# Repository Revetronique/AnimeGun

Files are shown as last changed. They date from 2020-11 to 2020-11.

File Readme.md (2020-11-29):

# アニメ銃 (ストロボスコープ式映写機)
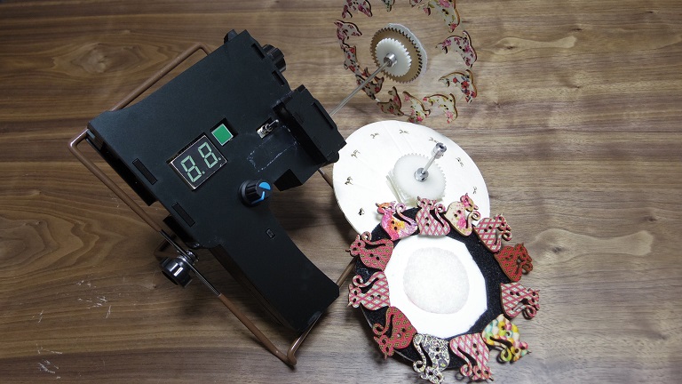
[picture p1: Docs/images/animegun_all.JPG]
Top Image

## 目次
- [アニメ銃 (ストロボスコープ式映写機)](#アニメ銃-ストロボスコープ式映写機)
  - [目次](#目次)
- [概要](#概要)
- [準備するもの](#準備するもの)
  - [本体](#本体)
  - [円板](#円板)
- [使い方](#使い方)
  - [ボタン一覧](#ボタン一覧)
  - [基本](#基本)
  - [詳細](#詳細)
    - [パラメータ設定](#パラメータ設定)
    - [設定モード](#設定モード)
    - [設定方法](#設定方法)
    - [ファームウェア書き換え](#ファームウェア書き換え)
- [免責事項](#免責事項)
- [開発者](#開発者)
# 概要
影絵でアニメーション映像を見せる映写機です。

電源を入れて、壁に向かって引き金のボタンを押すことで、壁にアニメーションが映し出されます。

アニメのコマを描いた円板をモーターで回し、LEDのストロボ発光でアニメーションを移す仕組みです。
# 準備するもの
## 本体
- Arduino UNO R3
- LED
  - 単色を想定(主に白色)
  - パワーLED(5V, 1W or 3W)にも対応
- 専用シールド
  - [回路およびプリント基板(Eagle用)](./Circuit)
  - 回路の詳細については、[回路についてのドキュメント](./Docs/Document_Circuit.md)を参照
- 筐体
  - アクリル板(厚さ3mm)をレーザーカッターで切断して、各パーツを積み重ねて制作
  - 筐体用のフレームは[Frameフォルダ](./Frame)を参照
  - 詳細は、[筐体についてのドキュメント](./Docs/Document_Frame.md)を参照
  - **試作段階のため、回路が筐体に収まらないなどの問題が生じる可能性があります**
- ACアダプタ(出力：DC12V, 1A以上)
## 円板
詳細は[円板についてのドキュメント](./Docs/Document_Plate.md)を参照。
# 使い方
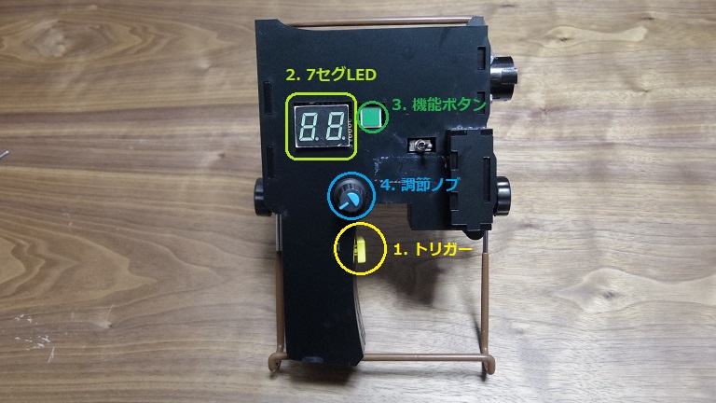
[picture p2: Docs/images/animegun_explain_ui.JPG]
Front Image

## ボタン一覧
1. **トリガー**：押すことでアニメを動かします(ストロボ発光+モーター駆動)
2. 7セグLED：設定モード([後述](#設定モード))やアニメに関するパラメータを表示
3. 機能ボタン：押すと設定モードを変更
4. **調節ノブ**：回すことでパラメータを調節

また、トグルスイッチでモーター回転の有効/無効を切り替えられます(右に倒すと有効)。ファームウェアの書き換え中など、モーターを回したくない時は左に倒してください。
## 基本
1. モーターにアニメ用の円板を付けます
2. 本体後ろのDCジャックに、上記のACアダプタから電源を供給
3. 銃口を壁に向けてトリガーを引くと、アニメーションが流れます
4. 調節ノブを回すと、アニメーションの速さを変えられます
## 詳細
### パラメータ設定
機能ボタンと調節ノブを使って、アニメーションに関する4種類のパラメータを調整できます。選択したパラメータと数値は7セグLEDで確認できます。
### 設定モード
パラメータの種類は以下の通り。
- sp(回転速度)：モーターの回転数(rpm)。数値は8~60
- dg(角度調節)：円板の角度調節。ずれの相殺に使います
- br(明るさ)：LEDの明るさ調整。0~25までの26段階
- fr(フレーム数)：アニメのコマ数
### 設定方法
起動時は、sp(回転速度)がセットされています。

ボタンを押すと、sp->dg->bf->fr の順に切り替わります。ボタンを押して0.5秒程度、選んだパラメータ名が7セグLEDに表示されます。

表示が数値に切り替わったら、調節ノブでパラメータを調節できます。
### ファームウェア書き換え
本体のファームウェア(Arduinoスケッチ)を書き換えたい場合は、背面のUSBコネクタでArduino IDEの入ったPCなどと接続します。ケーブルはUSB(ABタイプ)を使用します。
# 免責事項
- **使うときは人に向けないでください。特にパワーLEDを搭載する場合、失明の恐れがあります**
- 本体を振り回さないでください。ケガや破損の恐れがあります。
- モーターの回転中は、円板に触れないよう注意してください。思わぬケガの元となります。
- ファームウェア書き換え時は、書き込み用の機器と接続する前に、本体の電源を外してください。また、**接続中はトリガーを押さないでください**。
- 円板を付け替える際も、電源を外してから作業してください。
- 15V以上の電圧を絶対にかけないでください。
  - 出力電源は、12V,1A出力のACアダプタ推奨。
- 上記の項目の他、組み立て時や使用中などにおける利用者のあらゆる事故・不具合に対して、開発者は責任を負いません。

# 開発者
Revetronique
- [Web](https://revetronique.com/)
- [Twitter](https://twitter.com/Revetronique)
- [Instagram](https://www.instagram.com/revetronique/)

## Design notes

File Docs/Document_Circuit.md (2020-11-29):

# 回路について
## 概要
アニメ銃に組み込むArduino用シールドです。[Circuit](../Circuit)内にデータを保管してます。
## 回路図
本体用シールド

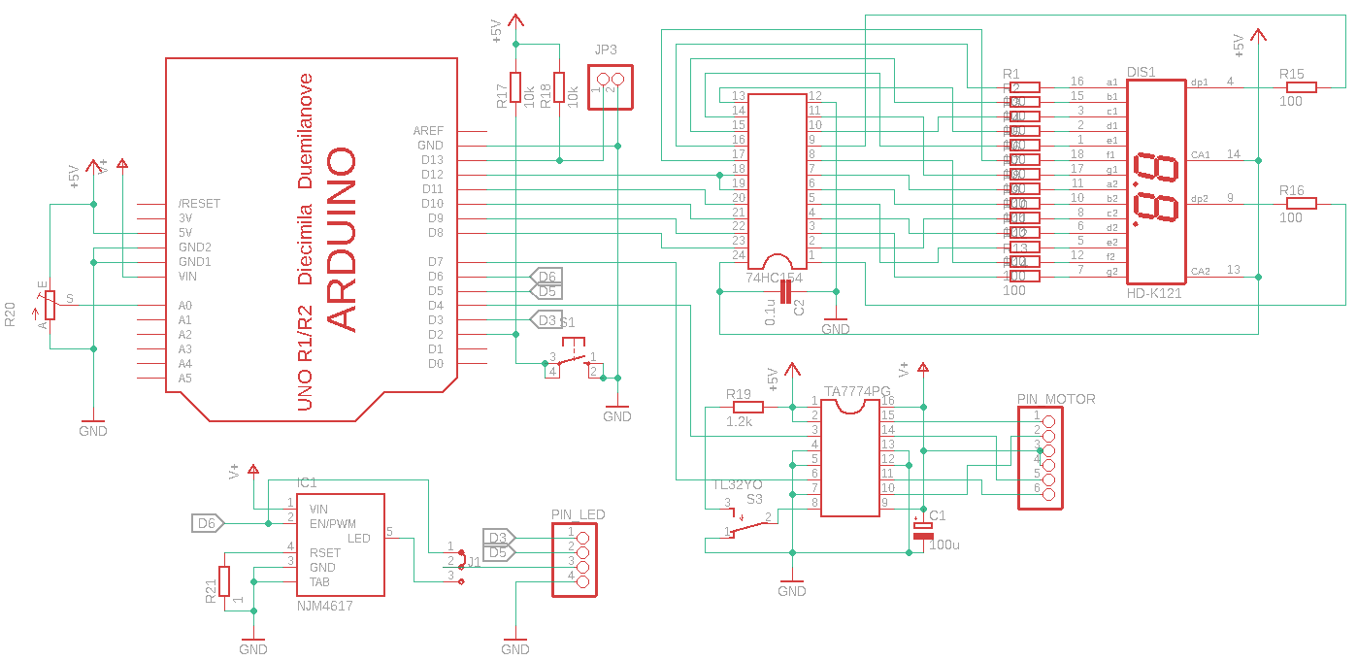
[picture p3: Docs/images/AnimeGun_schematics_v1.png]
Schematics


パワーLED用ハイサイドスイッチ

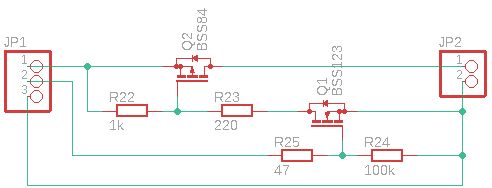
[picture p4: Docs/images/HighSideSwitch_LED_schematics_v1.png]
Highside

## 基板パターン(未使用)
基板配線

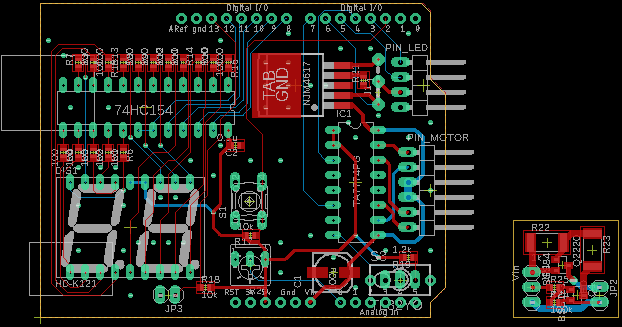
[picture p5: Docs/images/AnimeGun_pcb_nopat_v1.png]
PCB_nopat


ベタパターンあり

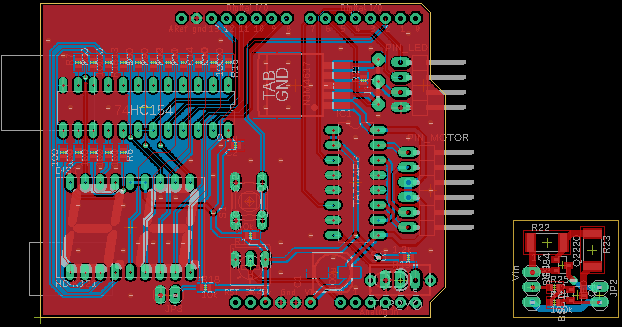
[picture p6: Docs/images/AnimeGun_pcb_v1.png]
PCB

## ファイル内容
- [回路図(Eagle)](../Circuit/AnimeGun_v1.sch)
- [パターン図(Eagle)](../Circuit/AnimeGun_v1.brd)
- [部品一覧](../Circuit/AnimeGun_bom_v1.txt)
## 使い方
1. Eagleでプロジェクトを新規作成
2. Eagleプロジェクトに上記ファイル2種類を読み込ませます
3. 必要に応じて、ライブラリをインストールしてください(Arduino、7セグLEDなど)
4. LEDドライバの部品のみ、既存ライブラリ(on-semiconductor.lbrのCAT4101)をもとに自作しました。CAT4101をコピーしてピン1と2を入れ替えるだけです。
## 注意点
- Eagleファイルは、試作した回路をもとに**後から作成した**ものです。試作品とは一部実装が異なる部分があります。
- PCBは、ユニバーサル基板で手付けした回路を元にEagleで書き起こしたもので、筐体との寸法や動作が合わない可能性があります
- J1はLEDドライバの実装を切り替えます
  - パワーLED用ドライバを実装する場合は、ピン2と3をショート
  - ドライバを実装しない/外部で接続する場合は、ピン1と2をショート
- LEDドライバの電流は、R21の抵抗値(=0.2/LED電流(A))で設定します。
- パワーLED用ハイサイドスイッチは、試作品で使用したLEDドライバへの電源制御用回路です(試作時は、秋月電子のLEDドライバ(3W)と出力ピン(D6)の間に接続)
  - シールドにLEDドライバを実装する場合は不要です
  - PWMで出力電圧を調整します
  - 電源は、ACアダプタの出力プラグを分岐するなどで接続してください
- Eagleで利用したタクトスイッチ(S1)では筐体に入らない可能性があります。秋月電子のボタン付タクトスイッチ(緑色)を実装してください
- 可変抵抗(R20)は、配線をのばして可変抵抗用の穴にさして固定します
- PIN_LEDはフルカラーLED用にPWMピン3つ(D3,5,6)をつないでいますが、通常は下から2番目のピンD6だけを使います

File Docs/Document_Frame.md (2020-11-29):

# 筐体について
## 概要
[Readme](../Readme.md)の写真にある筐体は、3mm厚のアクリル板をレーザーカッターでカットし、それぞれのパーツを積み重ねる形で作られています。
## ファイル内容
- [Adobeイラストレータファイル](../Frame/AnimeGun_frame.ai)
- [epsファイル(レーザーカッター出力用)](../Frame/AnimeGun_frame.ai)
## 使い方
1. epsファイルをレーザーカッターに読み込ませます
2. 3mm厚のアクリル板をレーザーカッターにセットします
3. それぞれの部品を貼りあわせます。接着剤はアクリサンデーが一般的です
## 注意点
- 試作段階のため、回路が筐体に収まらないなどの問題が生じる可能性があります
- パーツの貼り合わせる順番に注意してください
- パワーLED用の固定器具はありません。ご自身で作成してください

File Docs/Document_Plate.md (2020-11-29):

# アニメ用の円板について
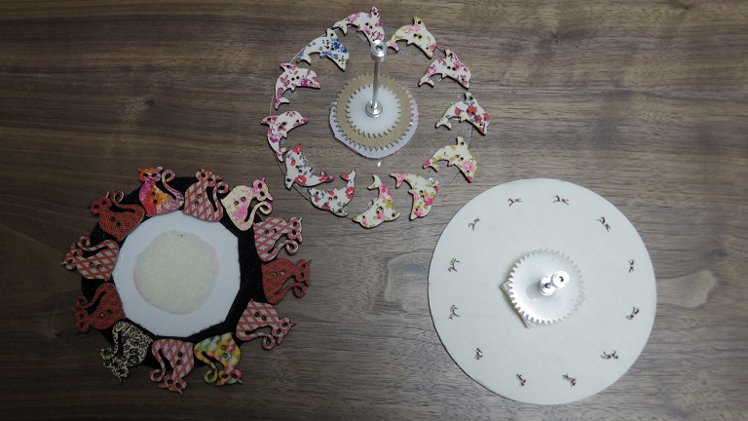
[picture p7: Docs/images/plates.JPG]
Front Image

## 概要
- サイズは直径12㎝
  - LEDの中心~モーター軸間の距離が 5cm のため
  - 筐体の変更などでLEDとモーターの距離が変われば、適切なサイズも変わります
- 素材は特に決まっていません
  - ただし、以下の条件を満たすものをお勧めします。
    - 自分で簡単に加工できる
    - 重すぎない
    - 立てたときに、曲がったりしなったりしない
  - なお制作時は、スチレンボードとアクリル板をそれぞれレーザーカッターで切り出しました。
## 準備
1. 直径12cmの円板を用意
2. アニメーションのパターン作成
   - パラパラ漫画の要領で、コマ数と絵のパターンを作ります
     - 12コマ位でパターンを用意するといい感じに配置できます
   - 「フェナキストスコープ」や「ゾートロープ」で画像検索するのもおすすめです
3. 円板にパターンを加工
   1. 光の像
      - 円板に等間隔でパターンの穴をくりぬきます
      - レーザーカッターなら円板自体も含めて綺麗に切り出せます。その場合、Adobeイラストレータなどでアニメのコマを円盤に配置したデータを作り、epsファイルを書き出す必要があります
      - 手作業の場合は、厚紙やスチレンボードなどをカッターで切るのが簡単かと思います
   2. 影絵
      - 各コマを切り取ったパーツを串につけ、モーター軸を中心に等間隔で並べると影絵ができます
      - アクリルなど透明な板に、小さなパーツを両面テープを使って貼り付ける方法もあります(画像中央の円板が該当)
4. シャフトと取り付け器具(カップリング)の設置
      - モーター軸は3mmなので、円板に取り付けるシャフトも3㎜幅がおすすめ
      - 円板の中心に、シャフトと同じ直径の穴をあけておきます
      - 円板にシャフトを差して固定します
      - シャフトの反対側に、モーターと結合するための部品をつけます
      - ジョイント用の部品は、[ストッパー](https://www.sengoku.co.jp/mod/sgk_cart/detail.php?code=4AJD-B5EA)や[インラインカラー](https://www.sengoku.co.jp/mod/sgk_cart/detail.php?code=5ALD-CJE7#)を使うといいでしょう
5. モーターとシャフトのジョイント

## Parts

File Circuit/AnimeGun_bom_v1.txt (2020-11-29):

Partlist exported from C:/Users/kokit/OneDrive/ドキュメント/EAGLE/projects/AnimeGun/AnimeGun-v1.sch at 2020/11/28 15:33

Part      Value          Device             Package        Description                                     MF MPN           OC_FARNELL OC_NEWARK POPULARITY SPICEPREFIX
74HC154                  DIL24-3            DIL24-3        Dual In Line                                                                          0                     
C1        100u           CPOL-EU153CLV-0605 153CLV-0605    POLARIZED CAPACITOR, European symbol                                                  5          C          
C2        0.1u           C-EUC0603          C0603          CAPACITOR, European symbol                                                            73         C          
DIS1      HD-K121        HD-K121            HDSP-R         LED DISPLAY                                                      unknown    unknown   0                     
IC1       NJM4617        NJM4617            TO263_5        1A Constant-Current LED Driver with PWM Dimming    CAT4101TV-T75 1718452    08R5264                         
J1                       J2X2MM             04C            Jumper switch 2 x 2.5 mm                                                                                    
JP1       Vin            PINHD-1X3          1X03           PIN HEADER                                                                            92                    
JP2       LED            PINHD-1X2          1X02           PIN HEADER                                                                            98                    
JP3                      PINHD-1X2          1X02           PIN HEADER                                                                            98                    
PIN_LED                  PINHD-1X4/90       1X04/90        PIN HEADER                                                                            9                     
PIN_MOTOR                PINHD-1X6/90       1X06/90        PIN HEADER                                                                            10                    
Q1        BSS123         BSS123             SOT23          N-CHANNEL MOS FET                                                                                           
Q2        BSS84          BSS84              SOT23          P-CHANNEL MOS FET                                                                                           
R1        100            R-EU_R0603         R0603          RESISTOR, European symbol                                                             70         R          
R2        100            R-EU_R0603         R0603          RESISTOR, European symbol                                                             70         R          
R3        100            R-EU_R0603         R0603          RESISTOR, European symbol                                                             70         R          
R4        100            R-EU_R0603         R0603          RESISTOR, European symbol                                                             70         R          
R5        100            R-EU_R0603         R0603          RESISTOR, European symbol                                                             70         R          
R6        100            R-EU_R0603         R0603          RESISTOR, European symbol                                                             70         R          
R7        100            R-EU_R0603         R0603          RESISTOR, European symbol                                                             70         R          
R8        100            R-EU_R0603         R0603          RESISTOR, European symbol                                                             70         R          
R9        100            R-EU_R0603         R0603          RESISTOR, European symbol                                                             70         R          
R10       100            R-EU_R0603         R0603          RESISTOR, European symbol                                                             70         R          
R11                      R-EU_R0603         R0603          RESISTOR, European symbol                                                             70         R          
R12       100            R-EU_R0603         R0603          RESISTOR, European symbol                                                             70         R          
R13       100            R-EU_R0603         R0603          RESISTOR, European symbol                                                             70         R          
R14       100            R-EU_R0603         R0603          RESISTOR, European symbol                                                             70         R          
R15       100            R-EU_R0603         R0603          RESISTOR, European symbol                                                             70         R          
R16       100            R-EU_R0603         R0603          RESISTOR, European symbol                                                             70         R          
R17       10k            R-EU_R0603         R0603          RESISTOR, European symbol                                                             70         R          
R18       10k            R-EU_R0603         R0603          RESISTOR, European symbol                                                             70         R          
R19       1.2k           R-EU_R0603         R0603          RESISTOR, European symbol                                                             70         R          
R20                      TRIM_EU-B25U       B25U           POTENTIOMETER                                                                                               
R21       1              R-EU_R0603         R0603          RESISTOR, European symbol                                                             70         R          
R22       1k             R-EU_R2512         R2512          RESISTOR, European symbol                                                             0          R          
R23       220            R-EU_R2512         R2512          RESISTOR, European symbol                                                             0          R          
R24       100k           R-EU_R0603         R0603          RESISTOR, European symbol                                                             70         R          
R25       47             R-EU_R0603         R0603          RESISTOR, European symbol                                                             70         R          
S1                       10-XX              B3F-10XX       OMRON SWITCH                                       B3F-1000      176432     36M3542   72                    
S3        TL32YO         TL32YO             TL3XYO         TINY SWITCH ON - MOM                                                                  1                     
TA7774PG                 DIL16              DIL16          Dual In Line / Socket                                                                 2                     
U1        ARDUINO-NOHOLE ARDUINO-NOHOLE     ARDUINO-NOHOLE Arduino Diecimila/Duemilanove

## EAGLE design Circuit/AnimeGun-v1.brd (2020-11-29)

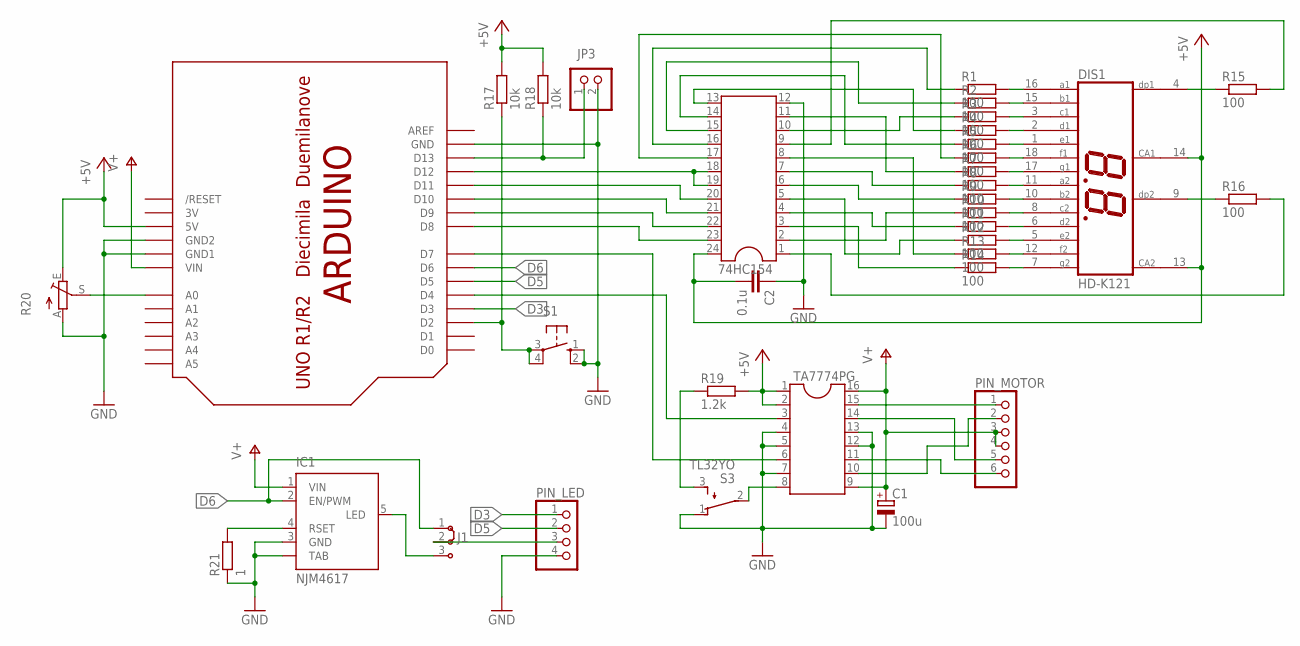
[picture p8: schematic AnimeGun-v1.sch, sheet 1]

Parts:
74HC154: DIL24-3
C1: 100u; 153CLV-0605
C2: 0.1u; C0603
DIS1: HD-K121; HDSP-R
IC1: NJM4617; TO263_5
J1: J2X2MM; 04C
JP3: PINHD-1X2; 1X02
PIN_LED: PINHD-1X4/90; 1X04/90
PIN_MOTOR: PINHD-1X6/90; 1X06/90
R1, R2, R3, R4, R5, R6, R7, R8, R9, R10, R12, R13, R14, R15, R16: 100; R0603
R11: R-EU_R0603; R0603
R17, R18: 10k; R0603
R19: 1.2k; R0603
R20: TRIM_EU-B25U; B25U
R21: 1; R0603
S1: 10-XX; B3F-10XX
S3: TL32YO; TL3XYO
TA7774PG: DIL16
U1: ARDUINO-NOHOLE

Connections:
3V: U1.3V
+5V: 74HC154.24, C2.2, DIS1.13 (CA2), DIS1.14 (CA1), R17.2, R18.2, R19.2, R20.E, TA7774PG.1, TA7774PG.2, U1.5V
D3: PIN_LED.1, U1.D3
D5: PIN_LED.2, U1.D5
D6: IC1.2 (EN/PWM), J1.1, U1.D6
GND: 74HC154.12, C1.-, C2.1, IC1.3 (GND), IC1.TAB, JP3.2, PIN_LED.4, R20.A, R21.1, S1.1 (S), S1.2 (S1), S3.1 (O), TA7774PG.4, TA7774PG.5, TA7774PG.7, TA7774PG.12, TA7774PG.13, U1.GND, U1.GND1, U1.GND2
unnamed: R17.1, S1.3, S1.4 (P1), U1.D2
unnamed: DIS1.16 (A1), R1.2
unnamed: DIS1.15 (B1), R2.2
unnamed: DIS1.3 (C1), R3.2
unnamed: DIS1.2 (D1), R4.2
unnamed: DIS1.1 (E1), R5.2
unnamed: DIS1.18 (F1), R6.2
unnamed: DIS1.17 (G1), R7.2
unnamed: DIS1.11 (A2), R8.2
unnamed: DIS1.10 (B2), R9.2
unnamed: DIS1.8 (C2), R10.2
unnamed: DIS1.6 (D2), R11.2
unnamed: DIS1.5 (E2), R12.2
unnamed: DIS1.12 (F2), R13.2
unnamed: DIS1.7 (G2), R14.2
unnamed: DIS1.4 (DP1), R15.1
unnamed: DIS1.9 (DP2), R16.1
unnamed: 74HC154.1, R16.2
unnamed: 74HC154.2, R10.1
unnamed: 74HC154.3, R14.1
unnamed: 74HC154.4, R11.1
unnamed: 74HC154.5, R12.1
unnamed: 74HC154.6, R9.1
unnamed: 74HC154.7, R8.1
unnamed: 74HC154.8, R13.1
unnamed: 74HC154.9, R15.2
unnamed: 74HC154.10, R3.1
unnamed: 74HC154.11, R7.1
unnamed: 74HC154.13, R4.1
unnamed: 74HC154.14, R5.1
unnamed: 74HC154.15, R2.1
unnamed: 74HC154.16, R1.1
unnamed: 74HC154.17, R6.1
unnamed: 74HC154.18, 74HC154.19, U1.D12
unnamed: TA7774PG.6, U1.D7
unnamed: 74HC154.20, U1.D11
unnamed: 74HC154.21, U1.D10
unnamed: 74HC154.22, U1.D9
unnamed: 74HC154.23, U1.D8
unnamed: TA7774PG.3, U1.D4
unnamed: JP3.1, R18.1, U1.D13
unnamed: S3.2, TA7774PG.8
unnamed: PIN_MOTOR.6, TA7774PG.11
unnamed: PIN_MOTOR.1, TA7774PG.15
unnamed: PIN_MOTOR.5, TA7774PG.14
unnamed: PIN_MOTOR.2, TA7774PG.10
unnamed: R19.1, S3.3 (S)
unnamed: R20.S, U1.A0
unnamed: IC1.4 (RSET), R21.2
unnamed: J1.2, PIN_LED.3
unnamed: IC1.5 (LED), J1.3
V+: C1.+, IC1.1 (VIN), PIN_MOTOR.3, PIN_MOTOR.4, TA7774PG.9, TA7774PG.16, U1.VIN

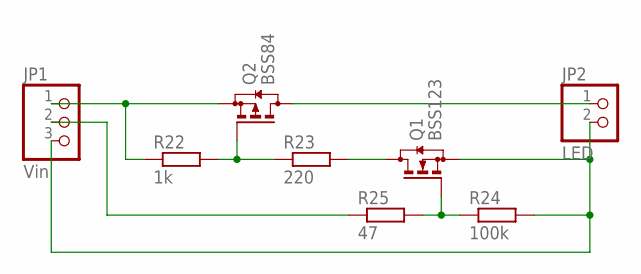
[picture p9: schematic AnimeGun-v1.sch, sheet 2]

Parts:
JP1: Vin; 1X03
JP2: LED; 1X02
Q1: BSS123; SOT23
Q2: BSS84; SOT23
R22: 1k; R2512
R23: 220; R2512
R24: 100k; R0603
R25: 47; R0603

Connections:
unnamed: Q2.1 (G), R22.2, R23.1
unnamed: JP1.1, Q2.2 (S), R22.1
unnamed: Q1.3 (D), R23.2
unnamed: JP2.1, Q2.3 (D)
unnamed: Q1.1 (G), R24.1, R25.2
unnamed: JP1.3, JP2.2, Q1.2 (S), R24.2
unnamed: JP1.2, R25.1

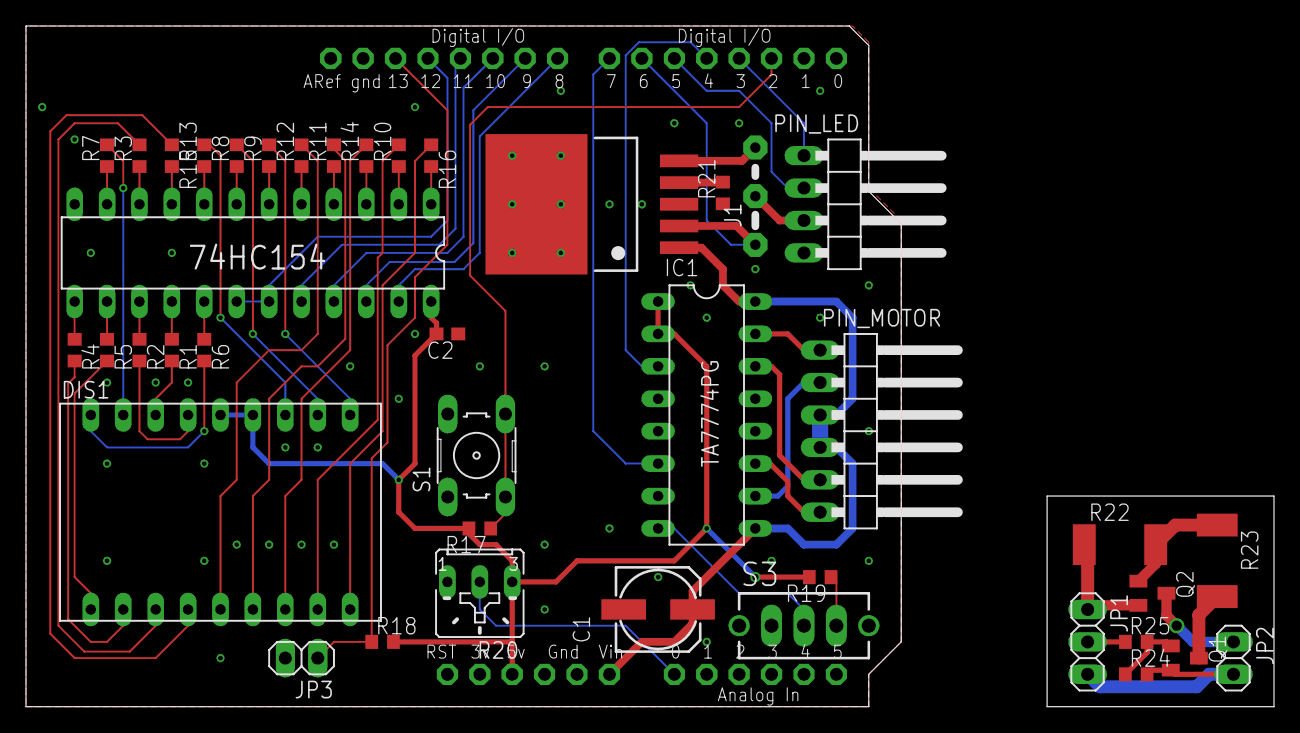
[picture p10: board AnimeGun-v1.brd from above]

Board: 2 copper layers, 68.6 x 53.3 mm, 42 parts (0 on the bottom side), 64 nets.

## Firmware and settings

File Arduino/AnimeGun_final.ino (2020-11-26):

#include <Stepper.h>
#include <math.h>

//#define FULLCOLOR

#ifndef FULLCOLOR
#define MODES 4
#else
#define MODES 5
#endif

#define STEPS 360  //ステッピングモーターのステップ数
#define DISPTIME 250  //7セグLEDの表示時間の半分<ms>

/*ピン設定*/
#define MTRPIN1 4
#define MTRPIN2 7
#define LEDPIN  6 //red
#define LEDPIN2 5 //green
#define LEDPIN3 3 //blue
#define LOGIC 8      //74HC154の入力ピンA<8~11, 12:Enable>
#define SWITCH  2     //ボタンスイッチ
#define TRIGGER 13    //トリガー

#define DIAL 0    //可変抵抗の入力ピン

/*7セグLEDの文字表示用変数*/
/*
    7         ***
  8   6      *   *
    3         ***
  5   2      *   *
    4    1    ***    *
*/
const byte CharSet[] PROGMEM =
{
  B11111010,  //A
  B10011110,  //B
  B11011000,  //C
  B00111110,  //D
  B11011100,  //E
  B11010100,  //F
  B11011010,  //G
  B10110110,  //H
  B00000010,  //I
  B00111010,  //J
  B11010110,  //K
  B10011000,  //L
  B11110010,  //M
  B00010110,  //N
  B00011110,  //O
  B11110100,  //P
  B11111100,  //Q
  B00010100,  //R
  B10001110,  //S
  B00011010,  //U
  B10111010,  //V
  B10111110,  //W
  B10110110,  //X
  B10101110,  //Y
  B01110100   //Z
};

const byte CharSetNum[] PROGMEM = 
{
  B11111010,
  B00100010,
  B01111100,
  B01101110,
  B10100110,
  B11001110,
  B11011110,
  B01100010,
  B11111110,
  B11101110
};
//byte char0 = B11111010;
//byte char1 = B00100010;
//byte char2 = B01111100;
//byte char3 = B01101110;
//byte char4 = B10100110;
//byte char5 = B11001110;
//byte char6 = B11011110;
//byte char7 = B01100010;
//byte char8 = B11111110;
//byte char9 = B11101110;

byte mode = 0;  //表示内容の変更<7セグ>
int timeCnt = 0;  //何秒経過したかを保存<モーター出力off時>
int rgb[] = {255, 255, 255};  //フルカラーLED専用の色調整

/*ステッピングモータ用ライブラリ*/
Stepper stepper(STEPS, MTRPIN1, MTRPIN2);

void setup()
{
  /*スイッチの設定*/
  pinMode(SWITCH, INPUT);
  pinMode(TRIGGER, INPUT);
  digitalWrite(LOGIC + 4, HIGH);
  
  /*ロジックICの設定*/
  for(int i = 0; i < 5; i++)  pinMode(LOGIC + i, OUTPUT);
  
  /*モーターの速度を指定*/
  stepper.setSpeed(30);
  
  attachInterrupt(0, modeChange, FALLING);
}

void loop()
{
  /*静的変数*/
  static int preValue = 0;
  static int brightness = 255;
  static int hue = 0;
  
  static int count = 0;    //モーターの累積ステップ数
  static int frames = 12;  //フレーム数
  
  static int spd = 0;
  
  /*AD変換*/
  int value = analogRead(DIAL);
  
  if(digitalRead(TRIGGER) == LOW){  //銃のトリガーを引く
  
    //7セグLEDの無効化
    timeCnt = 0;                    //7セグLED表示のリセット
    digitalWrite(LOGIC + 4, HIGH);  //7セグLEDに使うロジックICを無効化

    if(value != preValue){
      spd = map(value, 0, 1023, 8, 60);  //モーターの速度に変換
      stepper.setSpeed(spd);
    }
    
    //モーターを回転させる
    stepper.step(1);
    count++;
    
    //ストロボフラッシュの生成
    //モーターが一定の角度だけ回転する度に光るようにする
    //角度<ステップ数> = モーター1回転のステップ数 / アニメ1枚の総フレーム数
    if(count >= (STEPS / frames)){    // the motor steps each frame of anime
      // full color
      if(MODES == 5)  lightOn(rgb[0], rgb[1], rgb[2]);
      // single color
      else            lightOn(brightness, 0, 0);  //digitalWrite(LEDPIN, HIGH);
      count = 0;
    }
    else{
      lightOff();
    }
    
  }
  else{
    switch(mode){
      //モーターの速度変更  
      case 0:
        lightOff();
        
        if(value != preValue){
          spd = map(value, 0, 1023, 8, 60);  //モーターの速度に変換
          stepper.setSpeed(spd);
        }
        
        //7セグLEDの表示
        if(timeCnt > DISPTIME){  //0.5sを超えると
          Write7seg(spd / 10, 1);
          Write7seg(spd % 10, 0);
        }else{
          Write7seg('S', 1);
          Write7seg('P', 0);
          timeCnt++;
        }
        break;
      //角度調整<モーターのステップ角を変更>
      case 1:
        if(value != preValue){
          stepper.setSpeed(30);
          stepper.step(value - preValue);
          
          stepper.setSpeed(spd);
        }
        
        Write7seg('D', 1);
        Write7seg('G', 0);
        timeCnt++;
        
        break;
      //明るさ調整
      case 2:        
        if(value != preValue){
          brightness = (value >> 2) / 10;  //10bitの値を8bitに
          if(MODES == 5)  HSVtoRGB(hue, 255, brightness);
          else            analogWrite(LEDPIN, brightness);
        }
        
        //7セグLEDの表示
        if(timeCnt > DISPTIME){  //0.5sを超えると
          Write7seg(brightness / 10, 1);
          Write7seg(brightness % 10, 0);
        }else{
          Write7seg('B', 1);
          Write7seg('R', 0);
          timeCnt++;
        }
        break;
      //フレーム数調整
      case 3:
        lightOff();
        
        if(value != preValue){
          frames = map(value, 0, 1023, 1, 48);
        }
        
        //7セグLEDの表示
        if(timeCnt > DISPTIME){  //0.5sを超えると
          Write7seg(frames / 10, 1);
          Write7seg(frames % 10, 0);
        }else{
          Write7seg('F', 1);
          Write7seg('L', 0);
          timeCnt++;
        }
        
        break;
      //色調整
      case 4:
        if(value != preValue){
          hue = map(value, 0, 1023, 0, 359);
          HSVtoRGB(hue, 255, brightness);
        }
        
        //7セグLEDの表示
        if(timeCnt > DISPTIME){  //0.5sを超えると
          Write7seg(hue / 100, 1);      //100の桁
          Write7seg(hue / 10 % 10, 0);  //10の桁
        }else{
          Write7seg('C', 1);
          Write7seg('L', 0);
          timeCnt++;
        }
        
        break;
    }
  }
  
  preValue = value;
}

/*7セグLED用の表示関数, 計算上は表示で2msほど経過*/
void Write7seg(int value, byte digit){   // 数値,  桁数<0:1桁目, 1:2桁目>
  byte unit = pgm_read_byte_near(CharSetNum + value);
  
  for(int i = 0; i < 8; i++){
    if((unit >> i) & B00000001)  PORTB = (PORTB & B11100000) | (i + 8 * digit);
    else                         PORTB = (PORTB & B11100000) | B10000;
    delayMicroseconds(500); //delay(1);
    
  }
  
  //PORTB = (PORTB & B11100000) | B10000;
}

/*7セグLED用の表示関数<文字>, 計算上は表示で2msほど経過*/
void Write7seg(char moji, byte digit){
  byte unit = pgm_read_byte_near(CharSet + (byte)(moji - 'A'));
  
  for(int i = 0; i < 8; i++){
    if((unit >> i) & B00000001)  PORTB = (PORTB & B11100000) | (i + 8 * digit);
    else                         PORTB = (PORTB & B11100000) | B10000;
    delayMicroseconds(500); //delay(1);
  }
  
  PORTB = (PORTB & B11100000) | B10000;
}

/*HSVをRGBに変換する関数*/
void HSVtoRGB(int h, int s, int v){  //引数は、色相<0~359>、彩度<0~255>、明度<0~255>の順
  float f;
  int i, p, q, t;
  
  i = (int)floor(h / 60.0f) % 6;
  f = (float)(h / 60.f) - (float)floor(h / 60.0f);
  p = (int)round(v * (1.0f - (s / 255.0f)));
  q = (int)round(v * (1.0f - (s / 255.0f) * f));
  t = (int)round(v * (1.0f - (s / 255.0f) * (1.0f - f)));
  
  switch(i){
    case 0:  rgb[0] = v; rgb[1] = t; rgb[2] = p; break;
    case 1:  rgb[0] = q; rgb[1] = v; rgb[2] = p; break;
    case 2:  rgb[0] = p; rgb[1] = v; rgb[2] = t; break;
    case 3:  rgb[0] = p; rgb[1] = q; rgb[2] = v; break;
    case 4:  rgb[0] = t; rgb[1] = p; rgb[2] = v; break;
    case 5:  rgb[0] = v; rgb[1] = p; rgb[2] = q; break;
  }
  
  analogWrite(LEDPIN, rgb[0]);  //6ピンは赤
  analogWrite(LEDPIN2, rgb[1]);  //5ピンは緑
  analogWrite(LEDPIN3, rgb[2]);  //3ピンは青
}

void lightOn(int r, int g, int b){
  analogWrite(LEDPIN, r);  //6ピンは赤
  analogWrite(LEDPIN2, g);  //5ピンは緑
  analogWrite(LEDPIN3, b);  //3ピンは青
//  digitalWrite(LEDPIN, HIGH);  //6ピンは赤
//  digitalWrite(LEDPIN2, HIGH);  //5ピンは緑
//  digitalWrite(LEDPIN3, HIGH);  //3ピンは青
}

void lightOff(){
  digitalWrite(LEDPIN, LOW);  //LEDライトを消す
  digitalWrite(LEDPIN2, LOW);  //LED2ライトを消す
  digitalWrite(LEDPIN3, LOW);  //LED3ライトを消す
}

void modeChange(){
  mode = (mode + 1) % MODES;
  timeCnt = 0;
}

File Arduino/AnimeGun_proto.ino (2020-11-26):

/*
  MotorKnob
  
  A stepper moter follows the turns of a potetiometer
  (or other sensor) on analog input 0.
  
  https://www.arduino.cc/en/Reference/Stepper
  This example code is in the public domain.
  
  How to use stepper methods<instance stepper>
   Step C0 C1  <C0:pin1  C1:pin2>
     1  0  1
     2  1  1
     3  1  0
     4  0  0
     
  ２層励磁による駆動方法<軸を正面に見たときの左回転>
     X   ~X    Y   ~Y
     0    1    0    1
     1    0    0    1
     1    0    1    0
     0    1    1    0
*/

#include <Stepper.h>

// change this to the number of steps on your motor
#define STEPS 360
#define MTRPIN1 4
#define MTRPIN2 7
#define LEDPIN  6
#define SWITCH 13
//#define PERSTEP 30

int perStep = 30;

// create an instance of the stepper class, specifying
// the number of steps of the motor and the pins it's
// attached to
Stepper stepper(STEPS, MTRPIN1, MTRPIN2);  // specify the number of the steps pre round and the input pins

void setup()
{
  // set the speed of the motor to 30 RPMs
  //stepper.setSpeed(30);  // set the rotation speed of the motor<rpm>
  //stepper.setSpeed(60);  //the limit of the speed is 60 rpm <on 9V DC>
  
  pinMode(LEDPIN, OUTPUT);  //ストロボフラッシュ<LED>
  pinMode(12, OUTPUT);    //無くてもよい
  pinMode(SWITCH, INPUT);  //トリガー
  
  digitalWrite(12, HIGH);    //無くてもよい
}

void loop()
{
  static int preSpd = 0;  //前回のrpm<ストロボのfps=周波数>
  static int count = 0;   //ステップ数
  
  // set the speed of the motor
  // FPS:8,12,24,30,60 || 8~60
  int spd = analogRead(0);
  spd = map(spd, 0, 1023, 8, 60);
  stepper.setSpeed(spd);
  
  if(digitalRead(SWITCH) == LOW){
    // minus value makes inverse rotation.
    stepper.step(1);  // the count of the steps of the motor
    
    // make a strobe light
    // whose blinking speed syncronizes the speed of rotation of the motor
    count++;
    if(count >= perStep){    // the motor steps each frame of anime
      digitalWrite(LEDPIN, HIGH);
      count = 0;
    }
    else  digitalWrite(LEDPIN, LOW);
  }
}

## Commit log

2020-11-26 First Commit
    [add] add files: firmware(Arduino sketch), circuit schematics and housing frame
2020-11-29 Add Readme and document files
    [add] Readme.md and Documents
    [AnimeGun-v1.brd, AnimeGun-v1.sch]
